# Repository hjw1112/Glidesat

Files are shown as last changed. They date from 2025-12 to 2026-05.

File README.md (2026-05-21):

# Glidesat
Custom devboard with additional components for ESA cansat competition. 

This PCB is for ESA cansat competition and I made it because I thought premade devboards like rp pico is too big and limiting for my team's goal. So I made this devboard to save as much space as possible and to connect to CM4 module for image processing. 

It is most complex PCB project so it was quite difficult to work on it, but with some help from background knowledge from previous projects, i think it went smoothly :)

Here are screenshots of PCB Design

## PCB Design
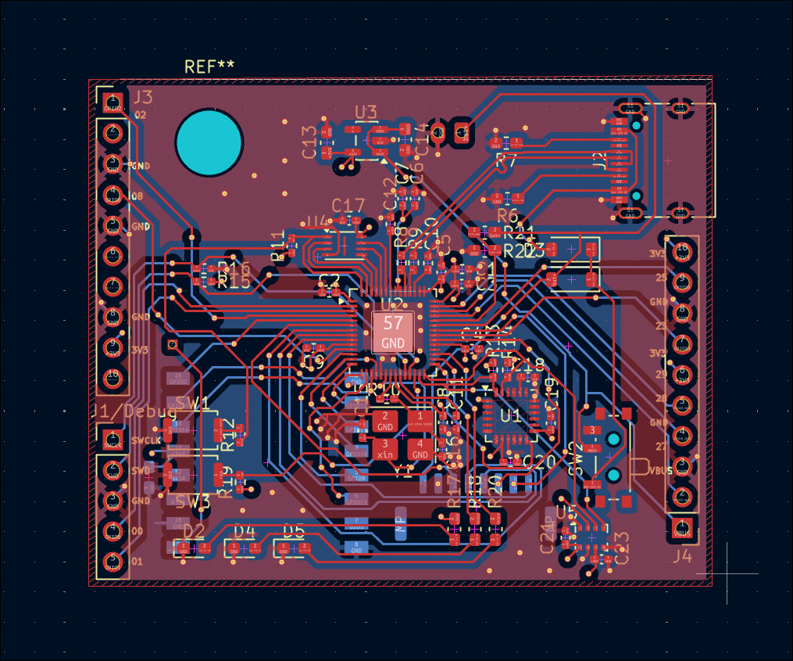
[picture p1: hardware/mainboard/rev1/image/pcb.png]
PCB


## Schematic
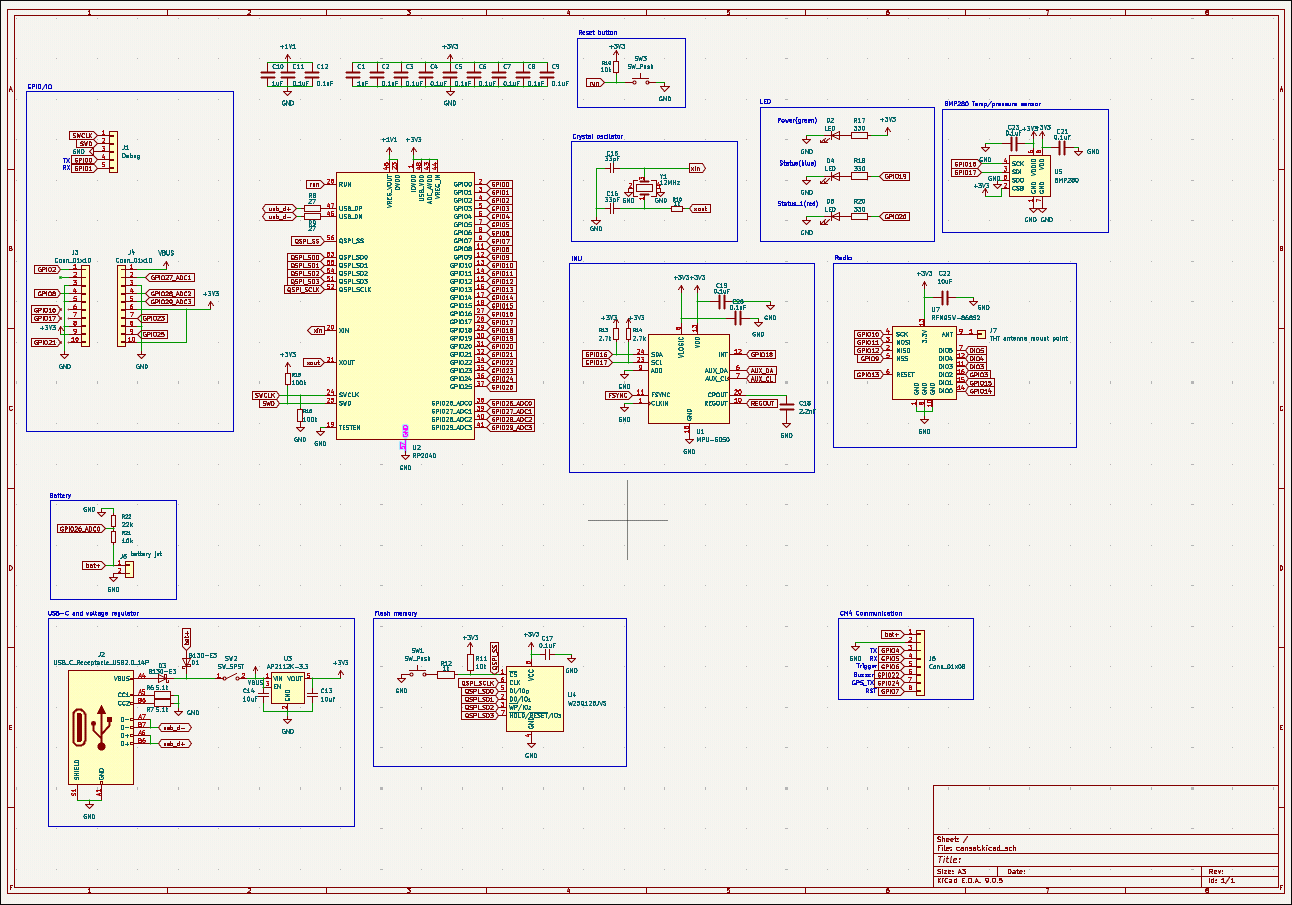
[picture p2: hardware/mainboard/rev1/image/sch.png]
Schematic


## 3D View
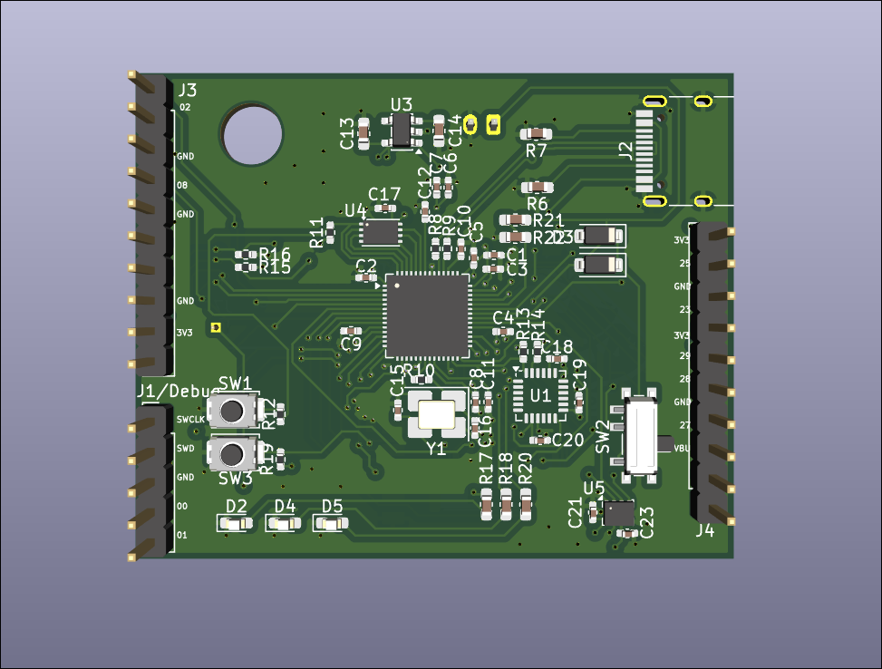
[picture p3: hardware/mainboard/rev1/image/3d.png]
3D View


## Soldered PCB

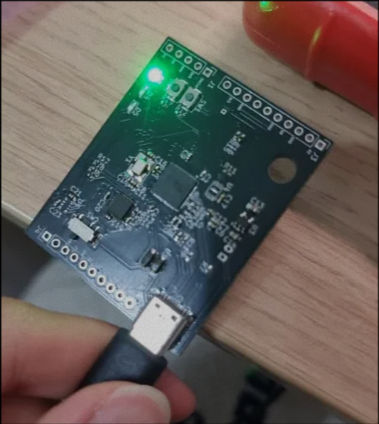
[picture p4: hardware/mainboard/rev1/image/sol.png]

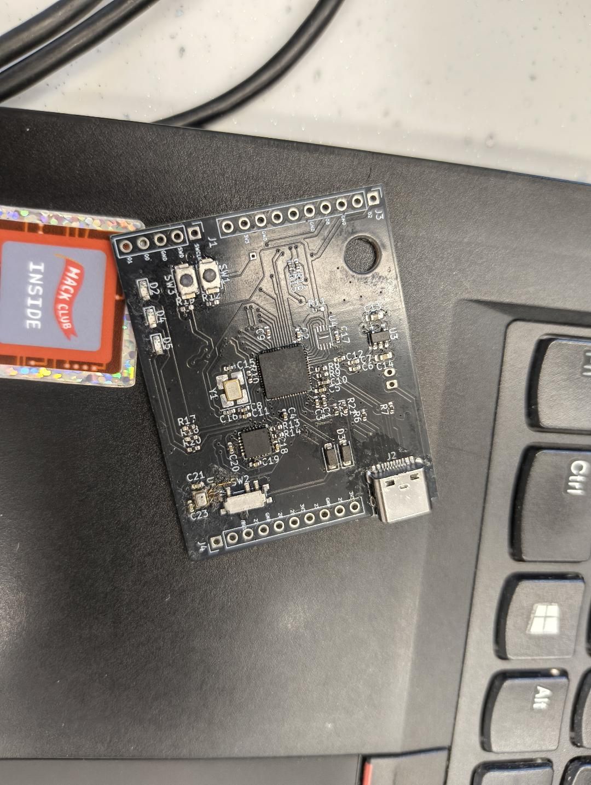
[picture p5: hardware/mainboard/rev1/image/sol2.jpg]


---

## BOM

| Component | Quantity |  Price | Net price | Source | | |
|:---|---:|:---|:---|:---|:---|:---|
| Capacitor 1uF | 100 |  0.0015 |  0.15 | https://www.lcsc.com/product-detail/C14445.html | | |
| Capacitor 0.1uF | 100 |  0.0011 |  0.11 | https://www.lcsc.com/product-detail/C1525.html | | |
| Capacitor 10uF | 50 |  0.0051 |  0.26 | https://www.lcsc.com/product-detail/C19702.html | | |
| Capacitor 33pF | 100 |  0.0030 |  0.30 | https://www.lcsc.com/product-detail/C70465.html | | |
| Capacitor 2.2nF | 100 |  0.0033 |  0.33 | https://www.lcsc.com/product-detail/C84703.html | | |
| B130-E3 | 10 |  0.0435 |  0.44 | https://www.lcsc.com/product-detail/C129191.html | | |
| LED(RED) | 100 |  0.0048 |  0.48 | https://www.lcsc.com/product-detail/C19171390.html | | |
| LED(GREEN) | 100 |  0.0047 |  0.47 | https://www.lcsc.com/product-detail/C19273151.html | | |
| LED(BLUE) | 100 |  0.0036 |  0.36 | https://www.lcsc.com/product-detail/C19171394.html | | |
| USB_C_Receptacle_USB2.0_14P | 5 |  0.1533 |  0.77 | https://www.lcsc.com/product-detail/C165948.html | | |
| Header pins | 10 |  0.0150 |  0.15 | https://www.lcsc.com/product-detail/C42431810.html | | |
| BM08B-GHS-TBT(LF)(SN) | 5 |  0.3074 |  1.54 | https://www.lcsc.com/product-detail/C133062.html | | |
| Resistor 5.1k 0603 | 100 |  0.0008 |  0.08 | https://www.lcsc.com/product-detail/C2907044.html | | |
| Resistor 27k 0402 | 100 |  0.0006 |  0.06 | https://www.lcsc.com/product-detail/C138017.html | | |
| Resistor 1k 0402 | 100 |  0.0006 |  0.06 | https://www.lcsc.com/product-detail/C106235.html | | |
| Resistor 10k 0402 | 100 |  0.0006 |  0.06 | https://www.lcsc.com/product-detail/C60490.html | | |
| Resistor 2.7k 0402 | 100 |  0.0007 |  0.07 | https://www.lcsc.com/product-detail/C138017.html | | |
| Resistor 100k 0402 | 100 |  0.0006 |  0.06 | https://www.lcsc.com/product-detail/C60491.html | | |
| Resistor 330 0603 | 100 |  0.0010 |  0.10 | https://www.lcsc.com/product-detail/C23138.html | | |
| Resistor 220 0603 | 100 |  0.0010 |  0.10 | https://www.lcsc.com/product-detail/C22962.html | | |
| Resistor 10k 0603 | 100 |  0.0010 |  0.10 | https://www.lcsc.com/product-detail/C98220.html | | |
| Resistor 22k 0603 | 100 |  0.0011 |  0.11 | https://www.lcsc.com/product-detail/C114065.html | | |
| SW_Push(XUNPU TS-1088-AR02016) | 10 |  0.0369 |  0.37 | https://www.lcsc.com/product-detail/C720477.html | | |
| SW_SPST(C&K PCM12SMTR) | 3 |  1.0445 |  3.13 | https://www.lcsc.com/product-detail/C221841.html | | |
| MPU-6050 | 3 |  5.9586 |  17.88 | https://www.lcsc.com/product-detail/C24112.html | | |
| RP2040 | 3 |  0.8250 |  2.48 | https://www.lcsc.com/product-detail/C2040.html | | |
| AP2112K-3.3 | 5 |  0.0803 |  0.40 | https://www.lcsc.com/product-detail/C23380830.html | | |
| W25Q128JVSIQ | 3 |  1.4281 |  4.28 | https://www.lcsc.com/product-detail/C97521.html | | |
| BMP280 | 2 |  5.2477 |  10.50 | https://www.lcsc.com/product-detail/C83291.html | | |
| RFM95W-868S2 | 1 |  9.5500 |  9.55 | https://www.tme.eu/sk/en/details/rfm95cw-868s2/rf-modules/hope-microelectronics/?brutto=1 | | |
| X322512MSB4SI | 10 |  0.0592 |  0.59 | https://www.lcsc.com/product-detail/C9002.html | | |
| | | | | | | |
| Shipping LCSC | | |  8.49 | | | |
| Discount | | |  6.00 | | Component total |  64.47 |
| Shipping from time.eu | | |  6.64 | | | |
| | | | | | | |
| PCB | | |  9.70 | JLCPCB | | |
| Shipping(GSDL) | | |  7.18 | | | |
| Tax | | |  2.58 | | PCB Total |  19.46 |
| | | | | | | |
| | | | | | | |
| TOTAL | | |  83.93EUR (about $98.82) | | | |

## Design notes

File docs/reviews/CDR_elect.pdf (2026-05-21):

## 7 Electronic Design

### 7.1 General Design

In the Preliminary Design Review (PDR), we used a 4-board system with Linux and GPS modules separated. However, we concluded that interference between RF modules is lower than interference with the Linux board. We managed to integrate the GPS module onto the mainboard. The number of boards remains the same, but the GPS module is now on the mainboard.

1. Mainboard – System control, sensor reading, radio communication, logic
2. Motor Control Board – Actuator control
3. Camera Board – High-resolution image capture
4. Linux Module – Commercial Linux module

This architecture separates the control system (mainboard), high-speed camera/Linux operation, and high-voltage motor control. This reduces electrical interference between sub-systems and improves communication reliability.

### 7.1.1 Design Evolution and Component Selection

At the start of the project, multiple MCUs were evaluated: Atmel ATmega series (Arduino equivalent), STM32, ESP32, and RP2040.

- Atmel chips were rejected due to insufficient processing power and memory to handle multiple peripherals reliably.
- STM32 and ESP32 were considered but were more power-hungry, more complex, and exceeded the performance needs of Glidesat.
- RP2040 was selected due to its dual-core processing, multiple communication interfaces, low power consumption, and strong community support. Despite QFN package soldering difficulties, the performance-to-power ratio justified its selection.

### 7.1.2 Board Design

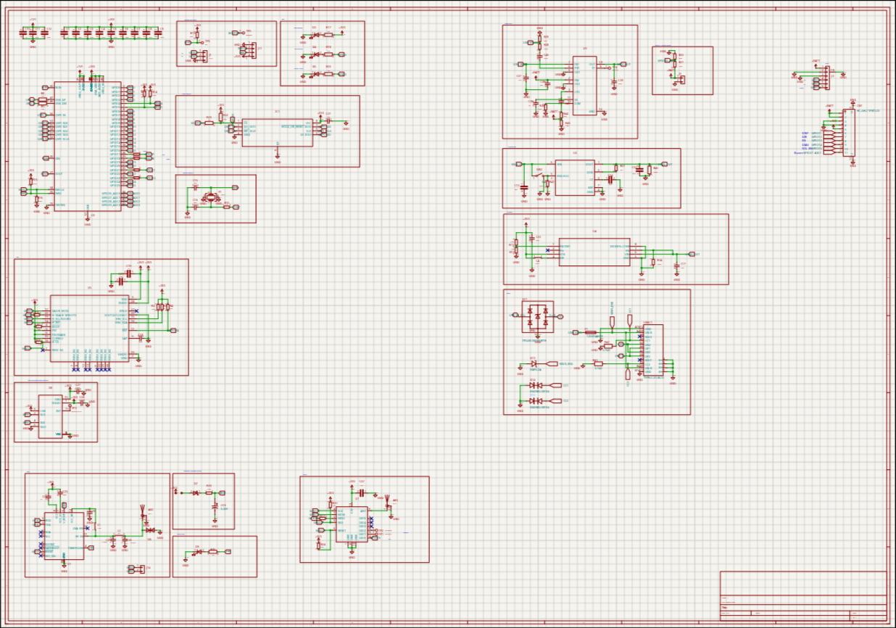
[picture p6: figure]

Figure 8: Schematic Design

The mainboard is a 4-layer PCB. Core processing is handled by the RP2040 SoC. Complementary components:

- Flash memory – W25Q128JVS
- Crystal oscillator – X322512MSB4SI

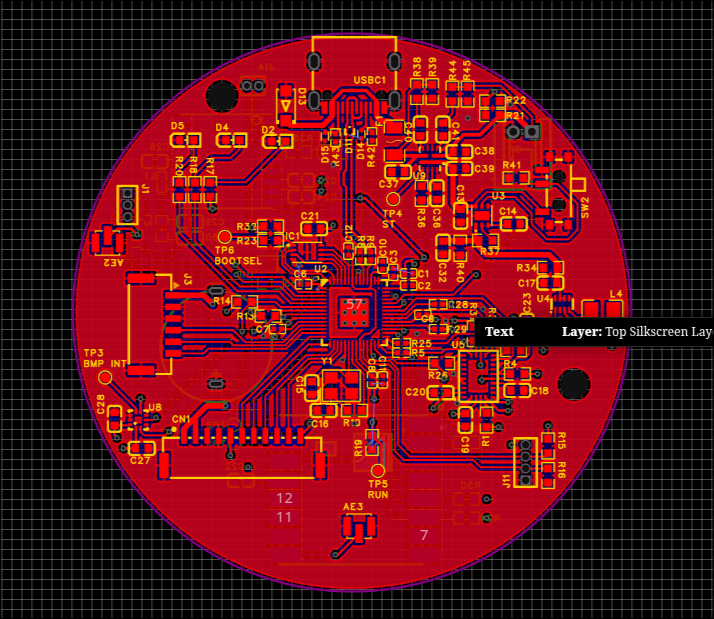
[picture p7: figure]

Figure 9: PCB Design

- Voltage regulator – AP2112K-3.3
- Power MUX – TPS2121RUXR
- Load switch – TPS22810DRVR
- Power MUX allows USB-C powering for flashing/testing.
- Load switch protects against high current draw which could damage a simple switch.
Sensor | Unit
Barometric Pressure Temperature IMU (Initial Measurement Unit) Battery Voltage Monitor | BMP388 BMP388 BNO085 GPIO ADC

Sensors are placed away from heat-generating components, with ventilation openings near them, to minimize thermal distortion.
IMU Selection: MPU-6050 was replaced with BNO085 to obtain 9-DOF measurements (magnetometer included) to prevent yaw drift. BNO085 offers internal sensor fusion, higher sampling rate, reduced MCU load, and additional data (gravity vector, linear acceleration) useful for landing detection and stable glider steering. ICM-20948 and others were considered but lacked magnetometers or required external fusion.
Barometric Sensor Selection: BMP388 was chosen for its precision (important for altitude monitoring without a camera), low pressure noise (useful during oscillating descent), high sampling rate ( 200 Hz), temperature compensation, compact size, dynamic pressure range (500 m– 9000 m), and low power consumption.

### 7.1.3 Radio Communications

RFM95W-868S2 LoRa transceiver is used via SPI to transmit telemetry to the ground station, including altitude, temperature, GPS coordinates, system status, and image capture status.

### 7.1.4 GPS

MAX-M10S-00B was selected for its multi-constellation support (higher accuracy), lower power consumption (20 mA vs 45 mA for older M10M), better sensitivity, and faster fix time.

### 7.1.5 Camera/Linux Board

For imaging, the Luckfox Pico Mini and MIS5001 5MP Wide-Angle Camera Module were chosen.

- Raspberry Pi Compute Module 4 was replaced due to size and weight.
- Camera resolution was reduced to 5 MP due to the Pico Mini’s 2-lane MIPI CSI limitation.
- High-resolution capture could not be done directly via RP2040 due to limited RAM, insufficient SPI bandwidth, and lack of MIPI CSI support.
- The Linux board triggers the camera via UART communication with the mainboard.

### 7.1.6 Motor Control Board

- Drives paraglider motors, regulates power for actuators, and includes a buzzer for recovery system (higher voltage requirement).
- Separation from mainboard prevents high-current electrical noise from affecting sensors or LoRa modules.
- Micro metal gear motor with encoder controlled via DRV8833 motor driver.

### 7.2 Power Supply

### 7.2.1 Power Source

Glidesat is powered by a rechargeable LiPo battery. Two options were considered: single-cell (3.7 V nominal) and dual-cell (7.4 V nominal).

- Dual-cell reduces current for the same power, improving wiring efficiency and allowing efficient buck conversion.
- Design considerations for dual-cell include charging circuit complexity and over-voltage protection.
- A dual-cell 2700–3000 mAh battery was selected to cover a 4-hour mission with safety margin ( 20 Wh total energy requirement).

### 7.2.2 Power Regulation

- Most electronics operate at 3.3 V (RP2040 and sensors) using a high-efficiency buck converter.
- Battery voltage monitored via mainboard ADC.
- Distribution via JST GH connectors to prevent disconnection.
- 3.3 V for mainboard components, raw 7.4 V to motor and Linux boards; 5 V regulated onboard for camera and motors.

### 7.3 Communication System

Glidesat communicates with the ground station via RFM95W-868S2 LoRa transceiver. The system supports bi-directional communication for telemetry and command reception.
Data transmitted from ;’[]:
- Altitude
- Temperature
- GPS coordinates
- Battery voltage

- System status
- Camera status

Data received by Glidesat:

- Motor direction
- Motor speed
- Recovery system activation

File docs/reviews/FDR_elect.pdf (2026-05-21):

## 7 Electronic Construction

### 7.1 System Overview

The electronic system of Glidesat consists of three custom-designed printed circuit boards (PCBs): a mainboard, a motor control board, and a Linux board. Off-the-shelf solutions were evaluated but rejected because their physical dimensions were not suitable for the 66 mm diameter CanSat form factor and they provided no isolation between high-current actuator paths and sensitive sensor/communication circuitry. Splitting the electronics across three boards allowed the us to fit all required functionality within the diameter limit while achieving electrical isolation between subsystems.3

### 7.1.1 Architecture

- Mainboard – flight computer, sensor, LoRa telemetry, GPS, data logging, power distribution.
- Motor control board – parafoil actuator drive, burn wire mechanism, buzzer recovery system.
- Linux board – Linux SBC, high-resolution imaging, onboard image storage.

This separation isolates the high-voltage, high-noise actuator paths on the motor board from the sensitive GPS, IMU, and LoRa circuitry on the mainboard. Each board operates on its own regulated power rail, providing independent fault domains.

### 7.1.2 Block Diagram

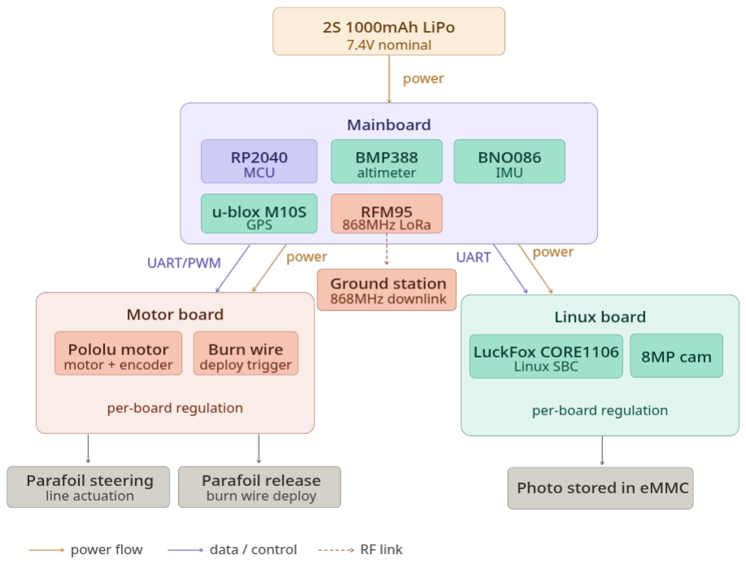
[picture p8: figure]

Figure 16: Block Diagram

### 7.2 PCB Design

### 7.2.1 Board Specifications

All boards are circular with a diameter of 60 mm and use M2.5 mounting holes positioned 15 mm from the centre of the board. The mainboard and Linux board use a four-layer stackup with the following layer assignment:

- L1 – signal

- L2 – ground plane
- L3 – power (with a dedicated region for raw battery voltage on the mainboard to improve current handling)
- L4 – signal

The motor board uses a two-layer stackup sufficient for its lower component density.

### 7.2.2 PCB Images

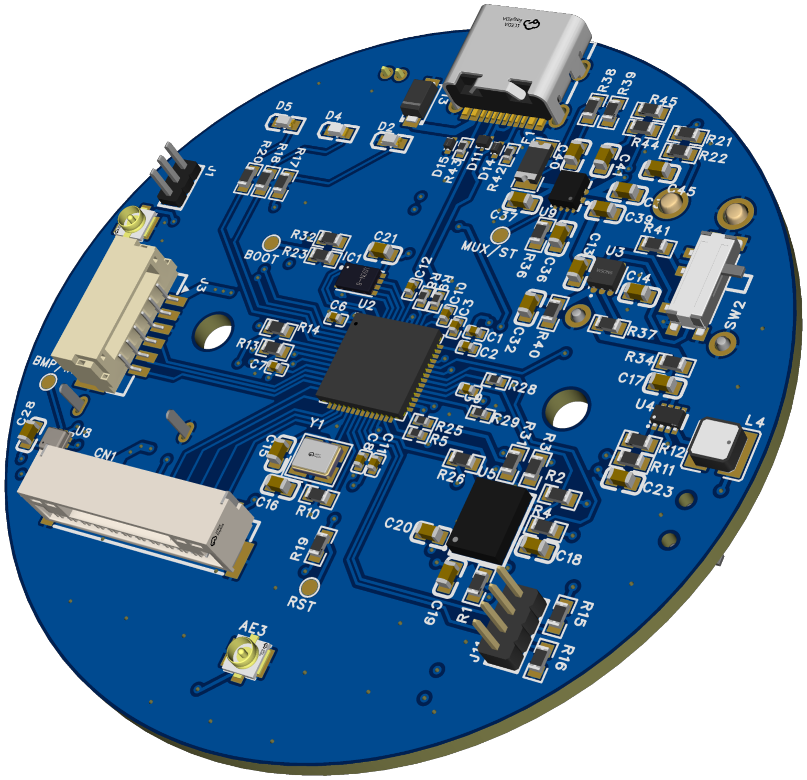
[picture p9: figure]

Figure 17: Mainboard

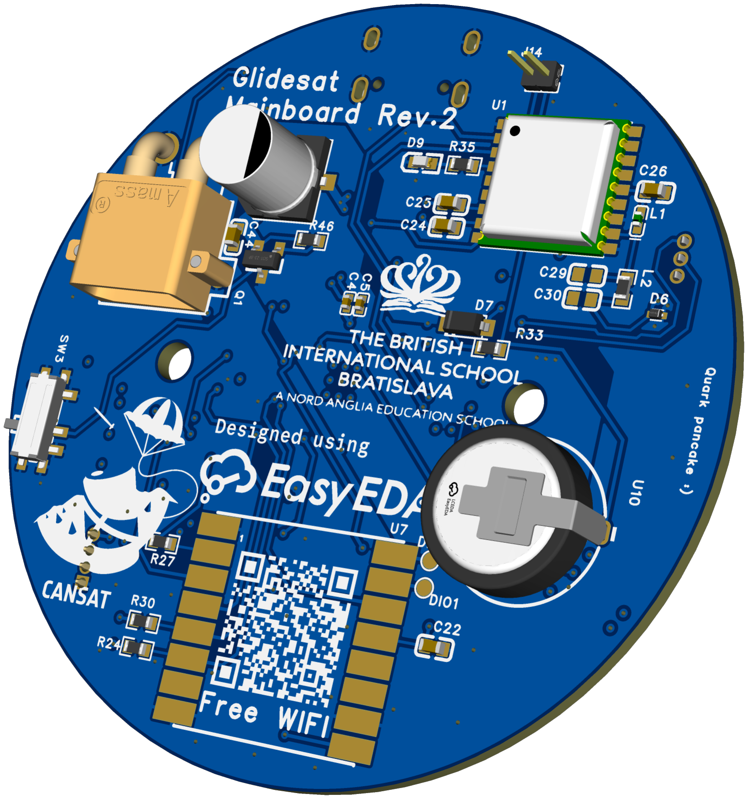
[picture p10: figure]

Figure 18: Mainboard(bottom)

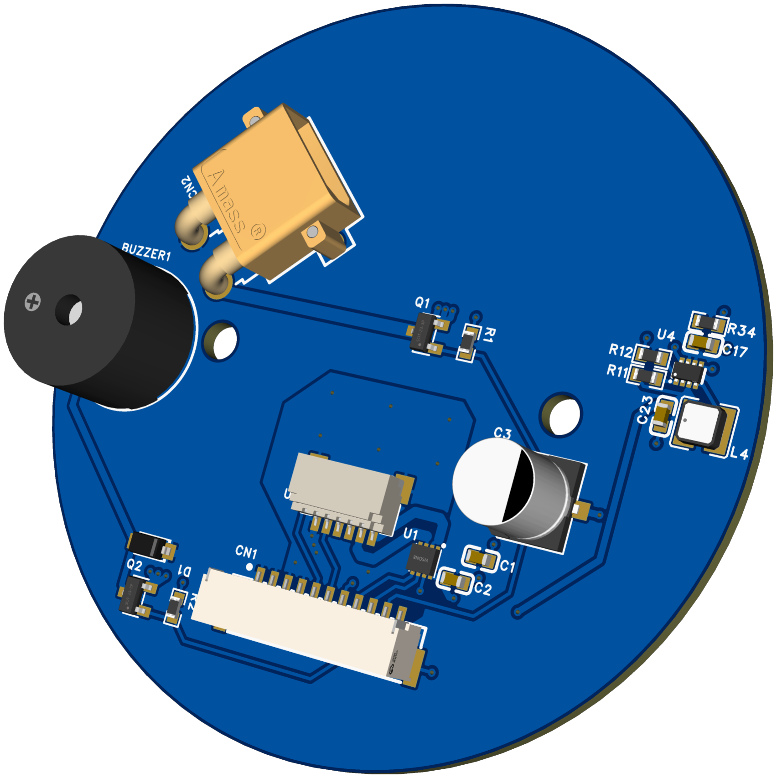
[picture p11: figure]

Figure 19: Motor Board

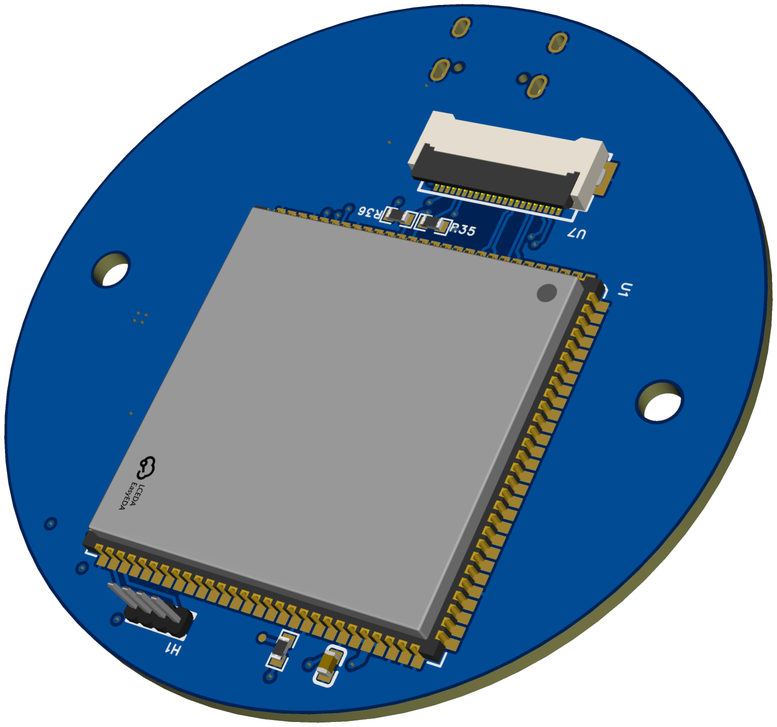
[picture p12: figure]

Figure 20: Linux Board

### 7.2.3 Board-to-Board Connections

JST-GH 1.25 mm pitch connectors were selected for all inter-board signal connections. The positive locking mechanism prevents disconnection under vibration during rocket ascent and mechanical shock on landing – a failure mode that unlatched connectors such as JST-PH or Dupont headers are susceptible to. All cables include strain relief at both ends.

### 7.3 Subsystem Descriptions

### 7.3.1 Flight Computer – RP2040

The RP2040 dual-core Cortex-M0+ SoC act as the flight computer.
Peripheral connections: SPI for RFM95W LoRa module and W25Q16JV flash memory; I2C for BMP388 and BNO086; UART for u-blox MAX-M10S and LuckFox Core1106; PWM for DRV8838 motor driver; GPIO ADC for battery voltage monitoring. A 12 MHz crystal oscillator provides the system clock reference.

### 7.3.2 Sensor Subsystem

Table 6: Sensor subsystem summary

Component | Function | Interface | Key Spec
BMP388 | Barometer, temperature | SPI/I2C | ±0.5 m altitude resolution
BNO086 | 9-DOF IMU | I2C | On-chip sensor fusion, quaternion output
u-blox M10S | GPS / GNSS | UART | Concurrent GNSS, 9 mA typical
IMX415 | Camera sensor | MIPI CSI | 8 MP, via LuckFox Core1106

BMP388 The BMP388 provides barometric altitude and temperature measurements. Its altitude resolution of ±0.5 m and low noise floor are important for monitoring the gliding descent without camera assistance. The higher sampling rate of up to 200 Hz and improved temperature compensation over its alternatives make it well suited to the Glidesat body that oscillates during descent.

BNO086 A 9-DOF IMU with on-chip sensor fusion was required because a 6-DOF IMU without a magnetometer causes yaw drift, which leads to mis-steering of the parafoil. The BNO086 outputs calibrated data directly, removing the need for an external fusion algorithm, reducing MCU load, and removing the risk of incorrect manual calibration.

u-blox MAX-M10S The MAX-M10S supports concurrent reception of GPS, GLONASS, Galileo, and BeiDou signals, improving position accuracy and fix reliability. At approximately 9 mA typical current consumption it draws significantly less power than the Neo-6M module used in earlier revisions. A 0.33 F supercapacitor on the mainboard maintains the module’s hot-start data and real-time clock during brief power interruptions, reducing position reacquisition time from approximately 30 s (cold start) to approximately 1 s (hot start).

### 7.3.3 Communication Subsystem

The RFM95W-868S2 LoRa transceiver operates at 868 MHz, which is within the licence-free ISM band across the European Union. The module is connected via SPI and implements a bi-directional link:

- Downlink (CanSat → ground station): altitude, temperature, GPS coordinates, battery voltage, system status, camera capture status.
- Uplink (ground station → CanSat): motor direction, motor speed, recovery system activation.

All telemetry is simultaneously logged to the W25Q16JV 16 Mbit flash memory, providing a complete flight data record independent of the radio link.
Antenna note: During PCB layout review it was identified that impedance matching for the RFM95W antenna trace was not implemented and the copper ground plane was not cleared under the antenna connector. This is expected to introduce approximately 1–3 dB of additional insertion loss due to signal reflection. The ground station uses a 13 dBi Yagi antenna, which provides sufficient gain margin to compensate for this loss. The link was confirmed operational during range testing. Also, a empty pi network with 0Ω resistor was implemented for post-impedance matching. So we can tune the impedance if we need extra range.

### 7.3.4 Actuation Subsystem

The motor board drives a Pololu 100:1 micro metal gearmotor with encoder using a DRV8838 single H-bridge motor driver. The 100:1 gear ratio was selected to provide sufficient torque to pull parafoil control lines under canopy load at operational descent speeds. The encoder provides closed-loop position feedback to the RP2040 control loop. The DRV8838 supports up to 1.8 A peak current, which is sufficient for the selected motor, and its WSON-8 2×2 mm package contributes to the compact board layout.
The burn wire deployment mechanism is triggered by a pair of AO3400A N-channel MOSFETs driven directly from RP2040 GPIO. The MOSFET pair allows reliable high-current switching at logiclevel gate voltage without the bulk and mechanical wear of a relay. Deployment confirmation is provided by monitoring current draw or encoder movement after trigger.
A buzzer is included on the motor board for post-landing recovery assistance. It is placed on the motor board because the higher supply voltage already present on that board is required for audible output level.

### 7.3.5 Imaging Subsystem

The LuckFox Core1106 runs a Linux operating system and interfaces with the IMX415 8 MP camera sensor via a two-lane MIPI CSI connection. Images are stored to the onboard eMMC. The LuckFox receives image capture commands from the RP2040 over UART and responds with capture status. Because Linux boot time is approximately 20–40 s, the Linux board is powered on and verified before launch to avoid mid-flight boot delay.

### 7.3.6 Power Subsystem

The system is powered by a 2S 1000 mAh LiPo battery with a nominal voltage of 7.4 V. A TPS2121 power multiplexer on the mainboard allows automatic switchover between battery and USB-C supply, enabling firmware development and sensor testing without connecting the flight battery.
Each board has a dedicated TPS629206 synchronous buck regulator providing the following voltage rails:
- Mainboard: 3.3 V for RP2040, sensors, and LoRa module.
- Motor board: 7.4 V raw battery voltage for motor and burn wire; 3.3 V regulated for logic.
- Linux board: 5 V for LuckFox Core1106.

Per-board regulation ensures that motor switching noise and current spikes on the motor board cannot affect the sensitive GPS, IMU, and LoRa rails on the mainboard. Battery voltage is monitored continuously by the RP2040 ADC using voltage divider. The XT30 battery connector is rated for 30 A continuous, providing a large margin over the 1.3 A peak system current draw.

### 7.3.7 Protective and Reliability Features

Several protective measures were implemented to improve robustness under the mechanical and electrical stresses of the mission environment.

Table 7: Protective and reliability features

Feature | Component | Protection provided
Overcurrent fuse | 1206T4A63V | Trips at 4 A on main power input; protects against
wiring faults and short circuits.
ESD protection | USBLC6-2SC6 | TVS
diode

Clamps electrostatic discharge on USB lines during ground handling and programming.

GPS backup power | 0.33 F supercapacitor | Maintains MAX-M10S hot-start data and RTC
during brief power interruptions; reduces reacquisition time from ∼30 s to ∼1 s.
Locking connectors | JST-GH 1.25 mm | Positive locking prevents vibration-induced dis-
connection during ascent and landing impact.

Battery connector
margin
XT30 | 30 A rating versus 1.3 A actual peak; eliminates
contact resistance and heating concern.

Per-board power isolation

TPS629206 per board Motor switching noise and fault conditions are contained to the motor board and cannot affect sensor or comms rails.

Decoupling capacitors

100 nF / 1 µF per IC Bulk and bypass capacitors on every IC supply pin suppress transient voltage spikes.

### 7.4 Component Selection

### 7.4.1 Selection Criteria and Weighting

All key component selections were evaluated against seven criteria using a weighted scoring matrix. The criteria and their assigned weights are listed in Table 8.

Table 8: Selection criteria and weights

Criterion | Weight | Rationale
Reliability | 3 | Flight-critical; no recovery if electronics fail mid-descent.
Performance | 3 | Directly affects mission success (navigation accuracy, link range).
Power consumption | 2 | Limited battery capacity; sleep modes required for 4 h operation.
Size | 2 | 60 mm board diameter constraint.
Ease of integration | 2 | Limited development time.
Cost | 1 | Secondary to reliability for this application.
Availability | 1 | All parts can be sourced from various sellers.

Scores from 1 to 5 were assigned for each criterion and each option. The weighted total is the sum of score × weight across all criteria. The chosen part corresponds to the highest weighted total in

every case.

### 7.4.2 Shortened Decision Table

Table 9: Electronics component selection — Mainboard

Component | Chosen part | Alternative(s) | Reasoning
MCU | RP2040 | STM32, ATmega | Dual Cortex-M0+ cores, large community, cheap, PIO for
custom peripherals
GPS | u-blox | MAX-
M10S

Neo-M8N, BN-880 Low power (9 mA), compact package, concurrent GNSS, proven reliability
IMU | BNO086 | BNO085, MPU-6050,
ICM-42688

On-chip sensor fusion (no extra MCU load), low idle power, interactive calibration
Barometer | BMP388 | MS5611, BMP280 | ±0.5 m resolution, lower noise floor, low power
LoRa | RFM95W-868S2 | SX1276, NRF24L01 | 868 MHz legal in EU, long range, module reduces RF lay-
out complexity
Flash | W25Q16JV | — | 16 Mbit external flash for telemetry and code; RP2040
lacks internal flash
Power MUX | TPS2121 | Diode, manual switch Automatic mux between battery and USB; allows devel-
opment without battery
Supercap | 0.33 F | — | Enables M10S hot start, reducing position acquisition
time
Load switch | TPS22810 | MOSFET, | bulky
switch

Limits excessive current; allows smaller switch with low current rating

Table 10: Electronics component selection — Motor Board, Linux Board, and General

Component | Chosen part | Alternative(s) | Reasoning

Motor Board

Motor driver | DRV8838 | L298N, TB6612 | Single H-bridge in WSON-8 package; 1.8 A peak,
sufficient for our motor
N-MOSFET | AO3400A ×2 | Relay, BJT | Reliable high-current switching for buzzer and burn
wire

Linux Board

Linux SBC | Luckfox Core 1106 | RPI | Zero | 2W,
ESP32-S3

Built-in MIPI CSI for camera; smaller and lower power than Pi Zero

General

ESD protection | USBLC6-2SC6 TVS Diode
— | Prevents electrostatic discharge damage during
handling
Buck regulator | TPS629206 | LM1117, AMS1117 | Higher efficiency than linear regulators
B2B connector | JST-GH | JST-PH, SH, etc. | Locking mechanism, reliability
Battery conn. | XT30 | JST, screw terminal | Rated for 30 A, massive safety margin, reliable

### 7.5 Power Budget

### 7.5.1 Current Consumption

Table 11 lists the estimated current draw for each component in active and sleep states. All values are datasheet typical figures unless noted as measured.

Table 11: Current consumption per component

Board | Component | Active (mA) | Sleep (mA)
5*Mainboard – 3.3 V | RP2040 | 25 | 2
| BMP388 | 3 | 0.1
| BNO086 | 6 | 1
| u-blox M10S | 25 | 15
| RFM95W | 30 | 0.2
2*Motor board – 7.4 V | DC motor | 150 | 5
| Burn wire | 0 | 0
2*Linux board – 5 V | LuckFox Core1106 | 400 | 10
| Camera (IMX415) | 50 | 0
Regulators (all boards) | 3× TPS629206 | 30 | 30
Total | | 719 | 63

### 7.5.2 Mission Profile Calculation

The mission is modelled as 30 min active followed by 3 h 30 min in sleep state. The active duration is a conservative worst-case estimate; typical active time is expected to be shorter.

Qactive = 0.5 h × 719 mA = 359.5 mAh Qsleep = 3.5 h × 63 mA = 220.5 mAh Qtotal = 359.5 + 220.5 = 580 mAh

Assuming a depth of discharge of 70 % to preserve battery longevity:

Qusable = 1000 mAh × 0.70 = 700 mAh

Qmargin = 700 − 580 = 120 mAh (17 %)

The 120 mAh safety margin is considered sufficient for the 4 h mission requirement.

### 7.5.3 Battery Selection

The Spektrum Smart G2 2S 1000 mAh 50C LiPo was selected. The reduction from the 2700 mAh specified at CDR was made possible by the sleep/active power analysis and change in cell number from 1 to 2, which showed that the LuckFox and motor consuming the majority of current are idle for most of the mission. The 50C discharge rating supports a peak current of 50 A, exceeding the 1.3 A actual peak draw (1.3C). The physical dimensions of the pack are compatible with the CanSat body.

### 7.6 Design Evolution and Revision History

### 7.6.1 Changes from PDR and CDR

Table 12 summarises all significant design changes made since the PDR and CDR submissions.

Table 12: Design evolution summary

Item | PDR/CDR | FDR | Reason
GPS loca- tion | Separate board | Mainboard | Mainboard placement keeps Linux board at bot- tom; GPS antenna faces top. LoRa/GPS interfer- ence negligible at achievable separation.
Camera SBC | RPi CM4 → LuckFox Pico Mini | LuckFox Core1106 | CM4 too large/heavy; Pico Mini lacked comput- ing power; Core1106 adds eMMC and robust form factor.
Camera sensor | Arducam 477P → MIS5001 5 MP
IMX415 8 MP | Higher resolution improves landing zone documen-
| | | tation.
IMU | MPU-6050 (6-DOF) | BNO086 | (9-
| | DOF) | Magnetometer prevents yaw drift; on-chip fusion reduces MCU load.
Barometer | BMP280 | BMP388 | ±0.5 m vs ±1 m resolution; lower noise; higher sample rate.
GPS mod- ule | Neo-6M | u-blox | MAX-
| | M10S | Concurrent GNSS; 9 mA vs 45 mA; faster fix time.

Motor
driver
DRV8833 | DRV8838 | Single H-bridge sufficient; smaller WSON-8 pack- age.
Battery | 1S 2700 mAh (CDR) | 2S 1000 mAh | Sleep/active analysis confirms sufficiency with 120 mAh margin; significant weight saving.
Board count | 4 boards (separate GPS) | 3 custom + 1 commercial | GPS integrated onto mainboard; camera module is commercial.

### 7.6.2 Revision 1 – Objectives and Findings

The objectives of Revision 1 were to validate the fundamental PCB design: RP2040 bring-up in multisensor configuration, SPI / I2C / UART interface verification, power regulation testing, and LoRa radio operation.

### 7.6.3 Revision 2 – Improvements

Revision 2 implements all lessons from Rev1 testing and upgrades all sensor components to their final flight versions.

Table 13: Test summary

Test | What was verified | Revision | Status
RP2040 bring-up | MCU boot, peripheral init | Rev1 | Pass
Sensor communication | I2C/SPI responses | Rev1 | Pass
LoRa link | Range, RSSI, packet loss | Rev1 | Pass
GPS fix | Fix time, accuracy | Rev2 | Pass
Motor + encoder | Closed-loop operation | Rev2 | Pass
Burn wire trigger | Fire time, current | Rev2 | Pass
Power measurement | Current draw vs estimate | Rev2 | Pass
Full system integration | 3-board combined test | Rev2 | Pass

### 7.7 Testing and Validation

### 7.7.1 Test Summary

### 7.8 Risk Assessment

### 7.8.1 Risk Table

Table 14: Electronics risk assessment

Risk | Likelihood Impact Mitigation

Motor board noise affecting sensors

Medium | High | Per-board power regulation and ground plane iso-
| lation.

Burn wire fails to trigger

Low | High | Bench-tested before flight; firmware watchdog
triggers backup after timeout if descent rate does
| not decrease.

LoRa link lost during
descent
Low | High | 868 MHz chosen for range; all telemetry logged to
onboard flash memory independently of radio link.
LuckFox fails to boot | Low | Medium All flight-critical functions reside on RP2040;
LuckFox failure does not abort the mission.

Battery undervoltage
during peak draw
Low | High | Decoupling capacitors on each board; motor stall
protection in firmware; 120 mAh safety margin.

Connector disconnection on landing

Low | High | JST-GH locking connectors; XT30 battery con-
nector; strain relief on all inter-board cables.

ESD damage during
handling

Medium Medium USBLC6-2SC6 TVS diode on USB lines; ESD handling procedures during integration.

Antenna impedance
mismatch
High | Low | Ground plane not cleared under antenna connec-
tor; estimated 1–3 dB loss compensated by 13 dBi Yagi at ground station; confirmed operational in
| range test.

### 7.8.2 Residual Risks

The antenna impedance mismatch remains unresolved in Revision 2. This is considered acceptable based on the range test results demonstrating reliable link operation, and the availability of a high-gain ground station antenna. Should field testing reveal insufficient range, the issue will be corrected with empty pi network.

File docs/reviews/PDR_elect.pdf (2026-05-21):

## 7 Electronic Design

### 7.1 General Design

The electronic system of Glidesat is divided into 4 boards. 1 mainboard and 4 sub-boards.

1. Mainboard - system control, sensor reading, radio communication, logics
2. Motor Control Board - actuator control
3. Camera Board – high resolution image taking and onboard data storage
4. GPS Module – commercial GPS module

This architecture allows us to separate the control system (mainboard), high speed camera operation, high voltage motor control, and high precision GPS. This separation reduces electrical interference between sub-systems and improves communication reliability. Communication between systems will use following standard interfaces: UART, I2C, SPI, PWM/GPIO.

### 7.1.1 Design Evolution and Component selections

In the beginning of the project, few MCUs were evaluated. Including the Atmel ATmega series (Arduino equivalent), STM32, ESP32, and RP2040. Atmel chips were rejected since they could not carry out multiple peripherals at the same time reliably, due to the lack of sufficient processing power and memory. STM32 and ESP32 chips were also considered but were found to consume more power, introduce unnecessary complexity, and exceed the performance requirements of our Glidesat application. The RP2040 SoC was selected as it offers dual-core processing power, multiple communication interfaces, low power consumption compared to higher end MCU such as STM32 or ESP32, and great community support and documentation. Although RP2040 is only available as QFN packages, which introduces soldering difficulties, the performance to power ratio advantages justifies the selection.

### 7.1.2 Board design

Complementary components: Flash memory – W25Q128JVS, Crystal oscillator - X322512MSB4SI, Voltage regulator – AP2112K-3.3

Sensor | Unit
Barometric pressure Temperature IMU (Initial Measurement Unit) Battery voltage monitor | BMP280 BMP280 MPU-6050 GPIO ADC

To minimise thermal distortion of environmental readings, sensors are placed in separate places with heat generating components, and ventilation opening will be placed near the sensors.
A LoRa transceiver is used for communication. It is connected via SPI and it is used to transmit telemetry data to the ground station. Including: Altitude, temperature, GPS coords, system status, image capture status. For GPS, the Neo-6M GPS module is used.
For camera module, we chose to integrate Raspberry Pi Compute Module 4(CM4) and Arducam 477P high-quality camera module for image capturing. In the beginning of the project, the camera system was planned to be controlled directly by RP2040 via SPI. However, this approach has been rejected since we needed a high resolution(10mp+) camera. The problem was limited RAM of RP2040 (and MCU in general), insufficient bandwidth of SPI for such high-resolution (No high res camera have SPI interface), and lack of native support of the MIPI CSI interface. To capture the high-resolution images, a Linux embedded computer was required. The Raspberry Pi Compute module 4 was therefore selected. The CM4 offers native MIPI CSI interface support, sufficient RAM, stable Linux camera drivers, and data storage via micro-SD card. CM4 will control the camera and trigger it by communicating with the mainboard via UART. There are two possible ways to operate CM4 are evaluated. The first option is operating continuously throughout the mission, and the second option

7

is turned on when needed using MOSFET. The first option can reduce power cycling and reliability but consume more power. However, the second option consumes less power, but it takes 20-40 seconds of time to boot the Linux system, and it is not highly reliable. Since reliability is a priority in this application, we decided to turn on the CM4 before launching and operate continuously throughout the flight.
The motor board will drive signals for paraglider motors, regulate power for actuators, and have a buzzer as part of the recovery system. The buzzer is added to the motor control board because it requires higher voltage which is already present in the board. Having a separated motor control board allows us to have high current paths separated from the mainboard and prevent electrical noises that might be present with high current paths from affecting sensors or LoRa modules, and it simplifies the PCB Design.

### 7.1.3 Prototype Mainboard Development (Mainboard Rev.1)

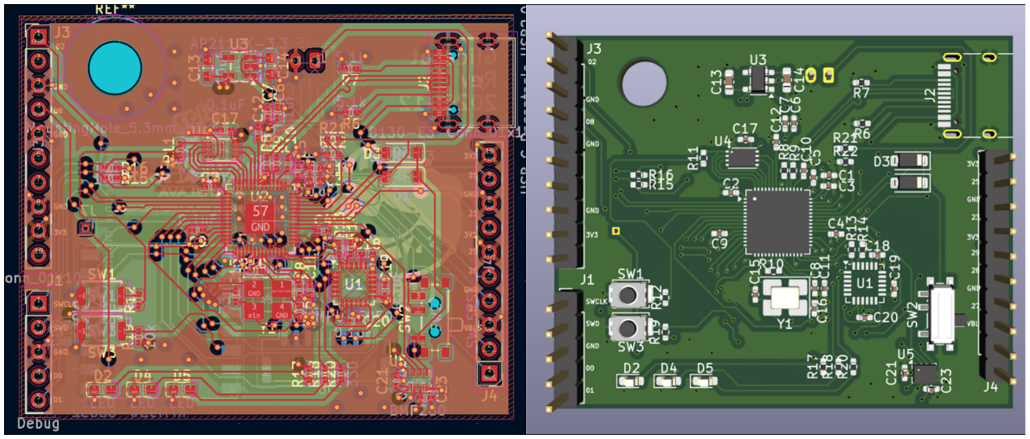
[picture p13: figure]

Figure 5: Prototype Mainboard

The first prototype of the mainboard was designed using Kicad, and we are currently waiting for the production.The objectives of Mainboard Rev.1 were to evaluate the general functionality of a designed PCB. Specifically, the RP2040 MCU in multi sensor configuration, verify SPI, I2C, and UART communication interfaces, test power regulation, test radio, etc. We spotted some flaws on PCB after submitting production via JLC PCB, but it should be okay since it is the first prototype.

### 7.1.4 Prototype Mainboard Development (Mainboard Rev.2)

After finishing Rev.1, we started to work on Rev.2 based on the mistakes we made in Rev.1. We planned pinout of the GPIO pins so we can keep pins organized and planned the board configuration. When we were working on Rev.1, we did not have clear board structure, so we only have a 01x08 JST connector in Rev.1
Also in Rev.1, we used MPU-6050 as our IMU. But after examining its capabilities, we found that it is not sufficient for controlling parafoil because it lacks a magnetometer which leads to the yaw drift. Thus, we will use 9-DOF IMU for Rev.2. Possibly MPU-9250 and ICM-20948.

### 7.2 Power Supply

The Glidesat is powered by a rechargeable lithium polymer battery system. Two options were evaluated. Single cell with nominal voltage 3.7V and double cell with 7.4V. Double cell systems offer higher voltage and reduced current for equal power consumption. However, it increases system complexity because of multiple voltage rails, has risk of overvoltage, more weight, and additional safety requirements for charging. Therefore, after evaluation, a single cell LiPo battery is chosen for Glidesat. Single cells are better since most electronics operate at 3.3V(RP2040, sensors, etc.), using a boost converter is simple and efficient, simplified charging, and reduced weight. Estimated power consumption: CM4 – 2W, Mainboard – 1W,Motor board and buzzer – 2W so total 5V . For mission of 1h 5W · 1h = 5Wh(safety margin of 2 − 5Wh)- therefore, a capacity between 2000mAh and 3000mAh battery is used. DC-DC boost converter generates higher voltage for CM4, actuators, and buzzer. A buck regulator generates 3.3V for RP2040. Battery voltage is monitored by the mainboard ADC.

8

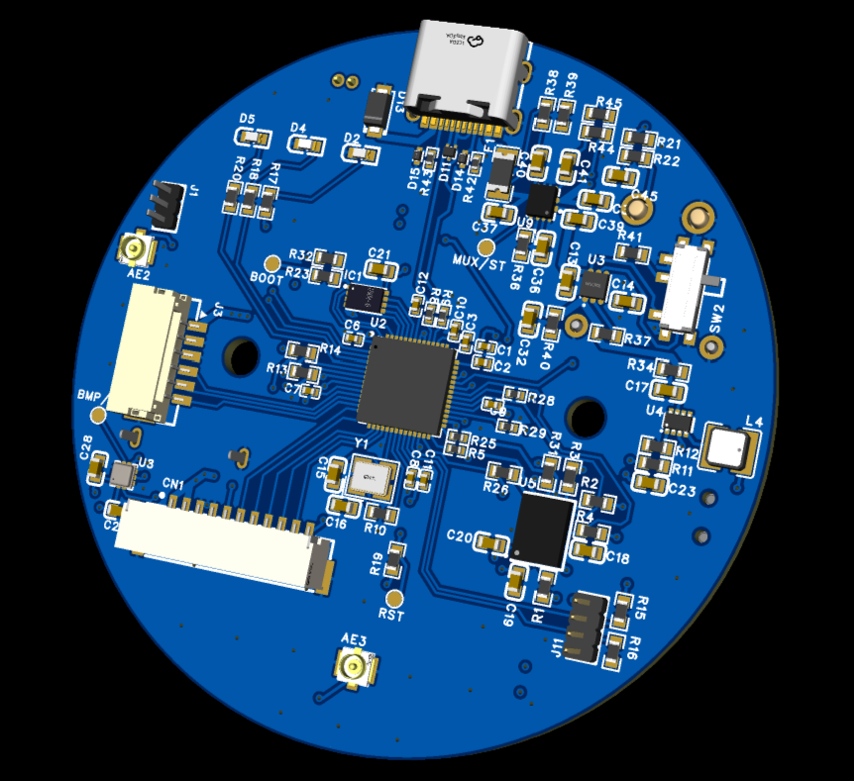
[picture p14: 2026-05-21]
hardware/mainboard/rev2/image/3d.png

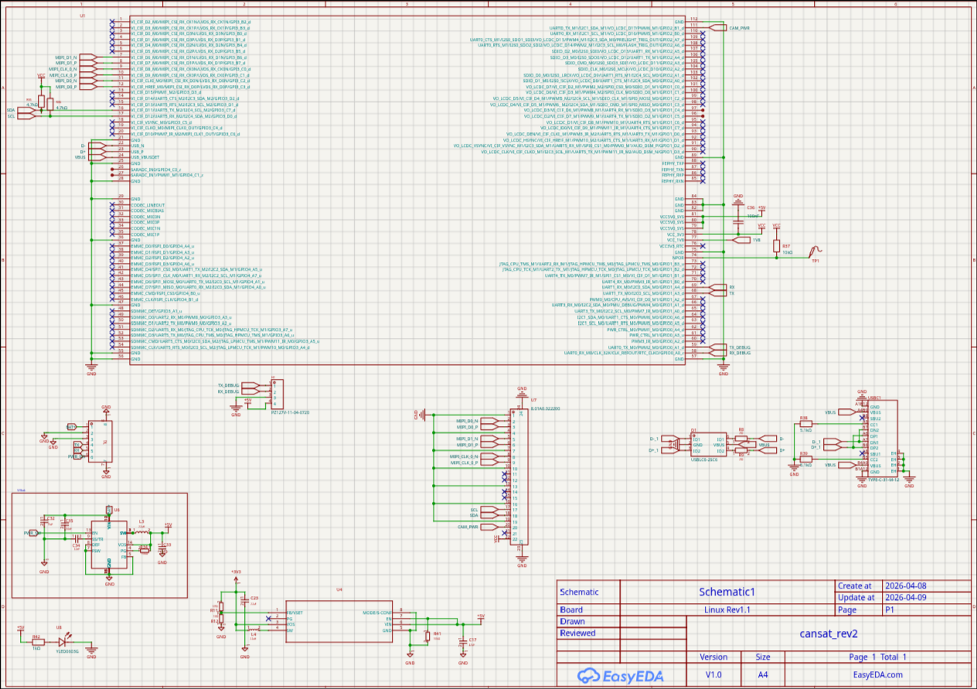
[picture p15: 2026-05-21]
hardware/linux-board/rev2/image/sch.png

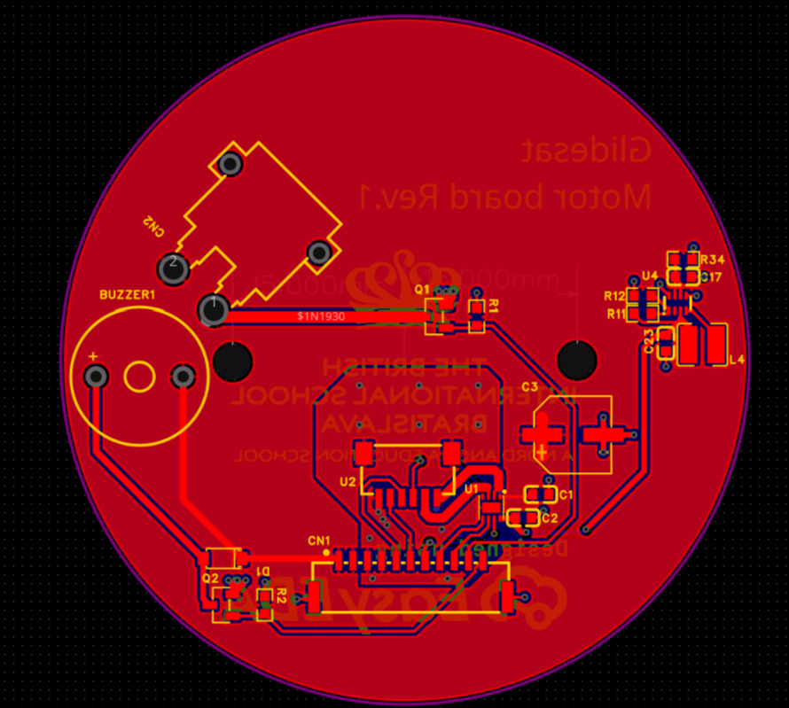
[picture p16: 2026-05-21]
hardware/motor-board/rev1/image/pcb.png

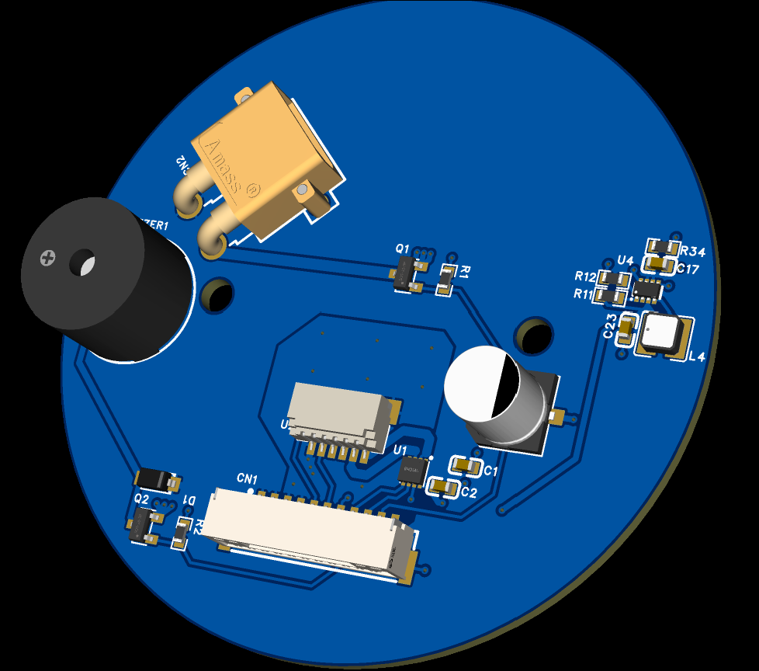
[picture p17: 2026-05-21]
hardware/motor-board/rev1/image/3d.png

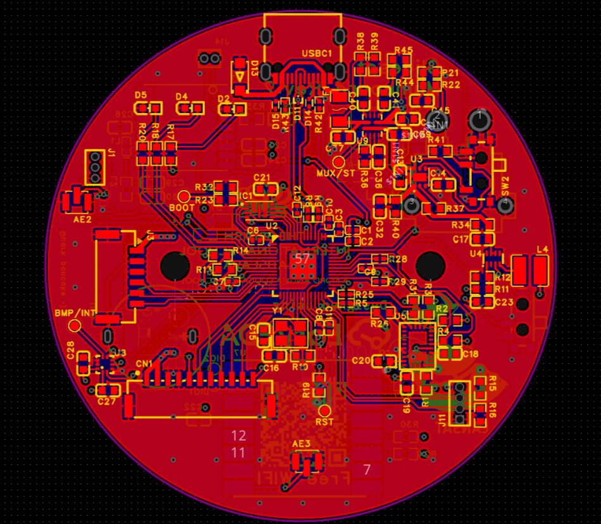
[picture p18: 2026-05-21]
hardware/mainboard/rev2/image/pcb.png

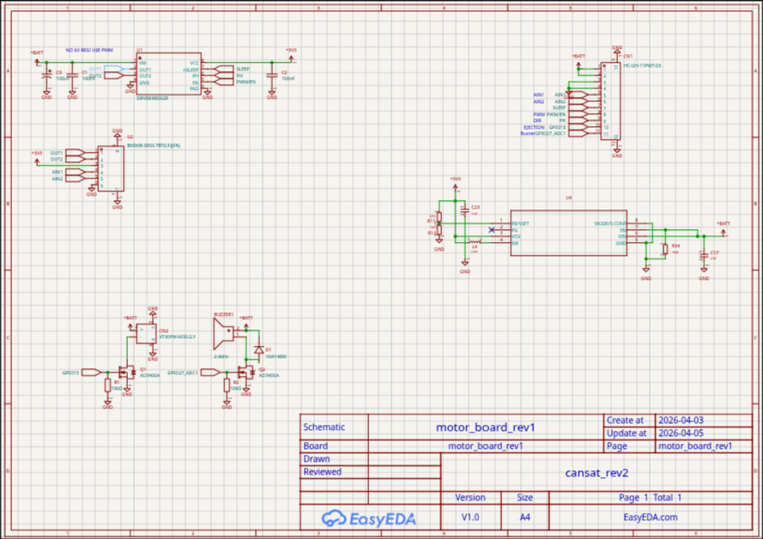
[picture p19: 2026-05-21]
hardware/motor-board/rev1/image/sch.png

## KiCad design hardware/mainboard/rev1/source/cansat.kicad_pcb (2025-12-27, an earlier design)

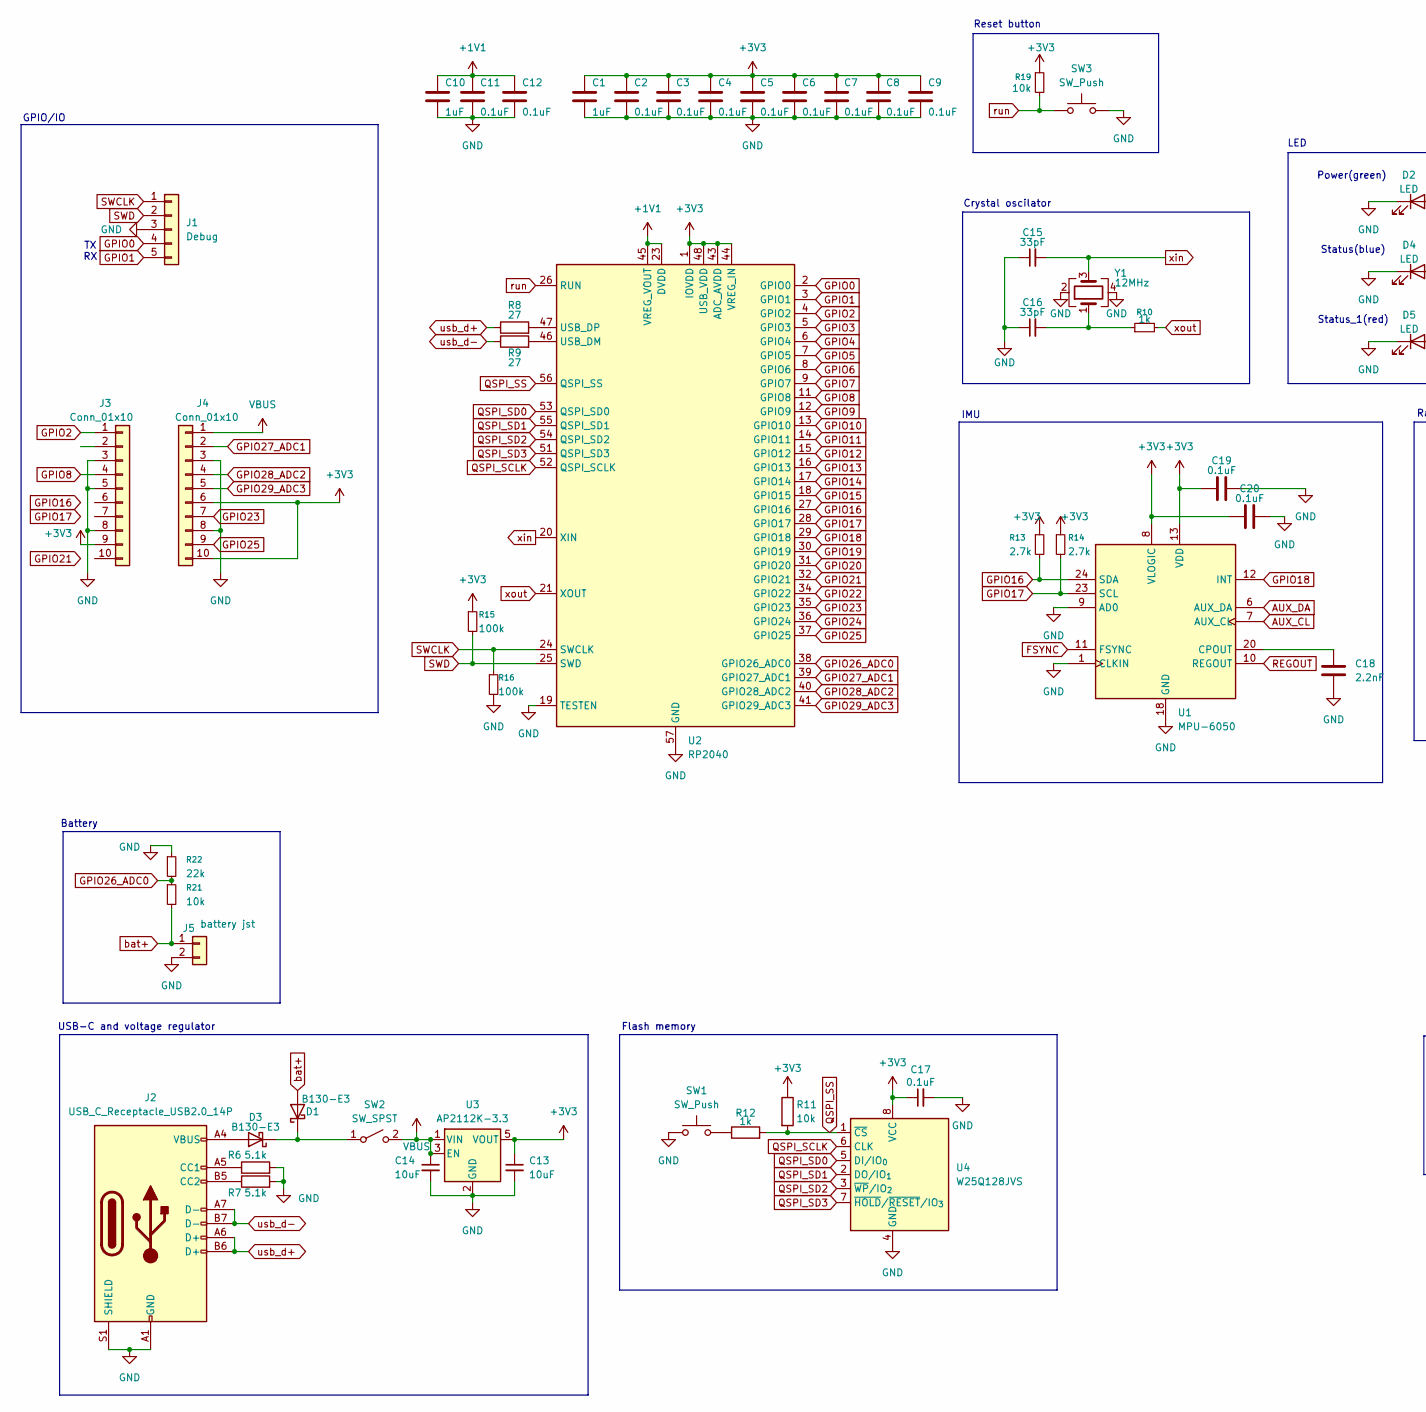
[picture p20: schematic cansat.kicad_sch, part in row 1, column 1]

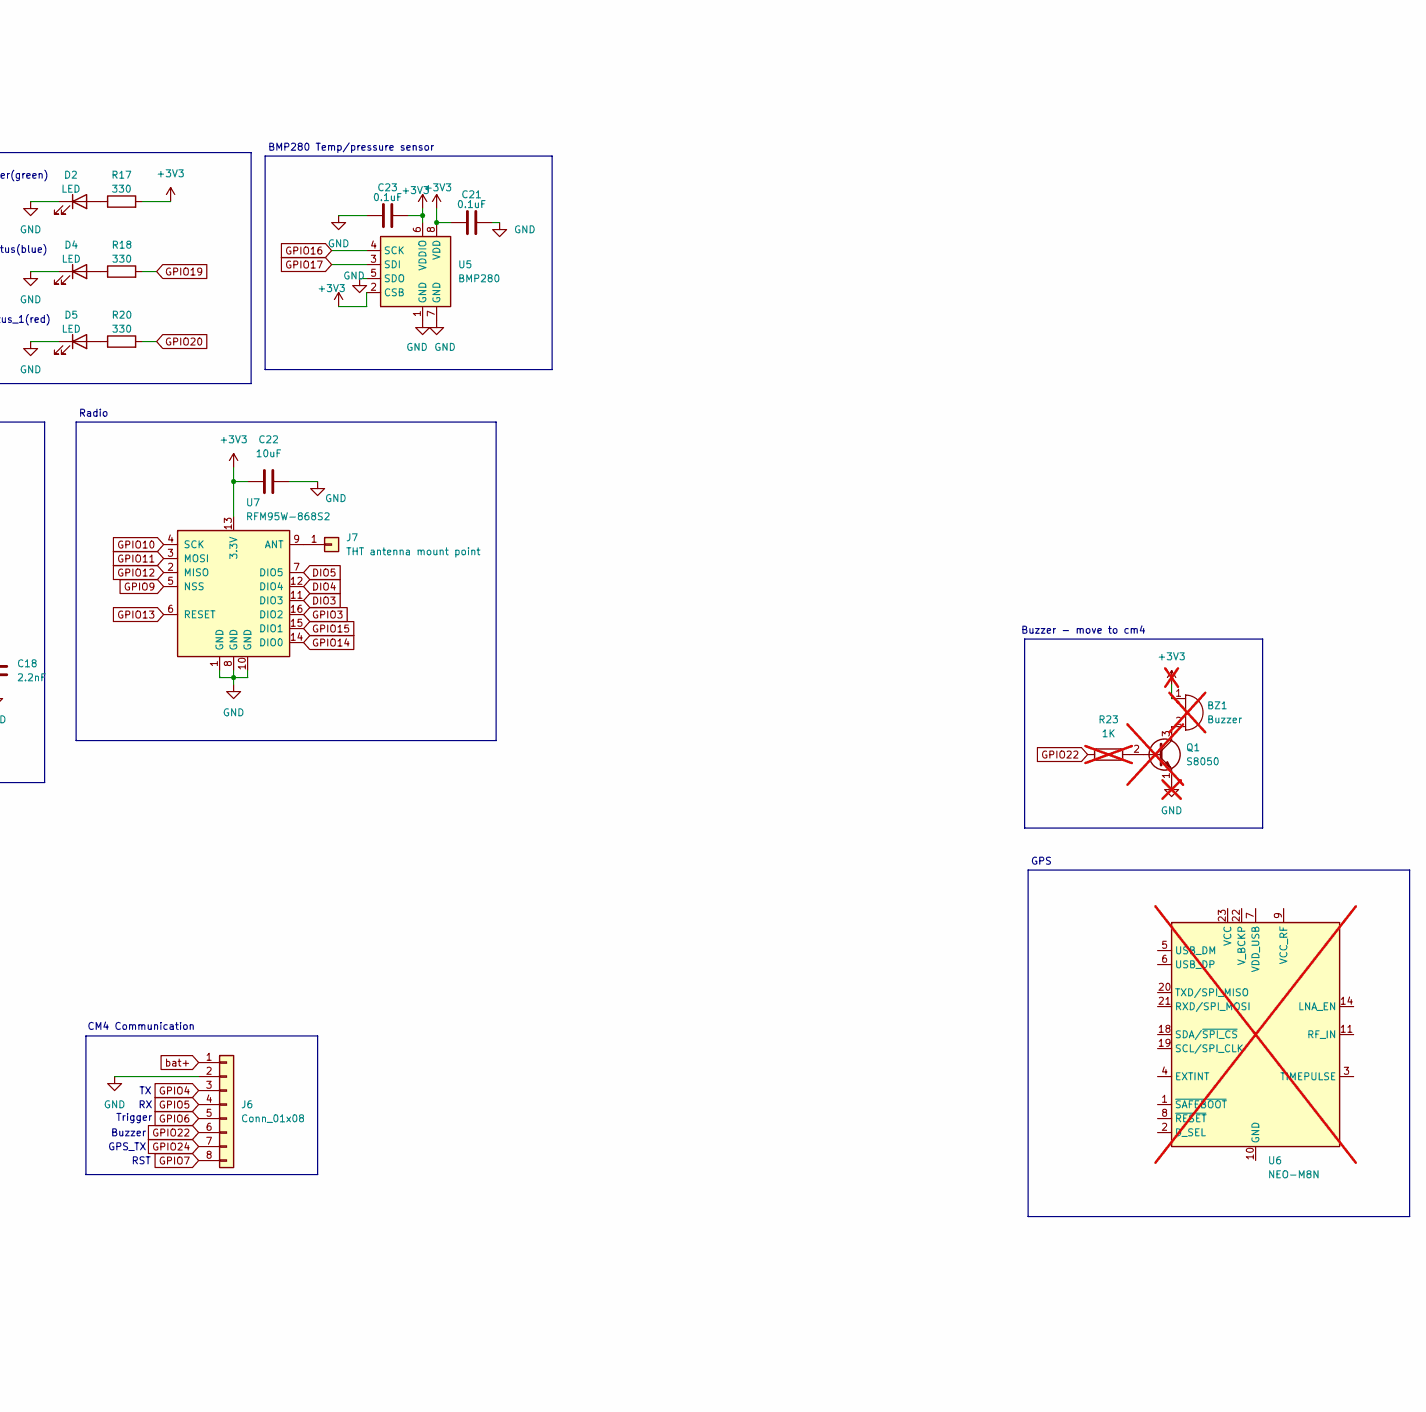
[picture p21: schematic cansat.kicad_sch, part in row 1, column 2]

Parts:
BZ1: Buzzer; not fitted
C1, C10: 1uF; C_0402_1005Metric_Pad0.74x0.62mm_HandSolder
C2, C3, C4, C5, C6, C7, C8, C9, C11, C12, C17, C19, C20, C21, C23: 0.1uF; C_0402_1005Metric_Pad0.74x0.62mm_HandSolder
C13, C14, C22: 10uF; C_0201_0603Metric_Pad0.64x0.40mm_HandSolder
C15, C16: 33pF; C_0402_1005Metric_Pad0.74x0.62mm_HandSolder
C18: 2.2nF; C_0402_1005Metric_Pad0.74x0.62mm_HandSolder
D1, D3: B130-E3; D_SOD-123
D2, D4, D5: LED; LED_0603_1608Metric_Pad1.05x0.95mm_HandSolder
J1: Debug; PinHeader_1x05_P2.00mm_Vertical
J2: USB_C_Receptacle_USB2.0_14P; USB_C_Receptacle_HRO_TYPE-C-31-M-12
J3, J4: Conn_01x10; PinHeader_1x10_P2.00mm_Vertical
J5: battery jst; JST_PH_S2B-PH-K_1x02_P2.00mm_Horizontal
J6: Conn_01x08; JST_GH_BM08B-GHS-TBT_1x08-1MP_P1.25mm_Vertical
J7: THT antenna mount point; PinHeader_1x01_P1.00mm_Vertical
Q1: S8050; TO-92_Inline; not fitted
R6, R7: 5.1k; C_0603_1608Metric_Pad1.08x0.95mm_HandSolder
R8, R9: 27; R_0402_1005Metric_Pad0.72x0.64mm_HandSolder
R10, R12: 1k; R_0402_1005Metric_Pad0.72x0.64mm_HandSolder
R11, R19: 10k; R_0402_1005Metric_Pad0.72x0.64mm_HandSolder
R13, R14: 2.7k; R_0402_1005Metric_Pad0.72x0.64mm_HandSolder
R15, R16: 100k; R_0402_1005Metric_Pad0.72x0.64mm_HandSolder
R17, R18, R20: 330; C_0603_1608Metric_Pad1.08x0.95mm_HandSolder
R21: 10k; C_0603_1608Metric_Pad1.08x0.95mm_HandSolder
R22: 22k; C_0603_1608Metric_Pad1.08x0.95mm_HandSolder
R23: 1K; not fitted
SW1, SW3: SW_Push; SW_Push_SPST_NO_Alps_SKRK
SW2: SW_SPST; SW_SPDT_PCM12
U1: MPU-6050; InvenSense_QFN-24_4x4mm_P0.5mm
U2: RP2040; QFN-56-1EP_7x7mm_P0.4mm_EP3.2x3.2mm
U3: AP2112K-3.3; SOT-23-5
U4: W25Q128JVS; Winbond_USON-8-1EP_3x2mm_P0.5mm_EP0.2x1.6mm
U5: BMP280; Bosch_LGA-8_2x2.5mm_P0.65mm_ClockwisePinNumbering
U6: NEO-M8N; ublox_NEO; not fitted
U7: RFM95W-868S2; XCVR_RFM95W-868S2
Y1: 12MHz; Crystal_SMD_3225-4Pin_3.2x2.5mm_HandSoldering

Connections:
+1V1: C10.1, C11.1, C12.1, U2.23 (DVDD), U2.45 (VREG_VOUT), U2.50 (DVDD)
+3V3: BZ1.1 (+), C1.1, C2.1, C3.1, C4.1, C5.1, C6.1, C7.1, C8.1, C9.1, C13.1, C17.1, C19.1, C20.1, C21.1, C22.2, C23.2, J3.9, J4.6, J4.10, R11.1, R13.1, R14.1, R15.1, R17.2, R19.1, U1.8 (VLOGIC), U1.13 (VDD), U2.1 (IOVDD), U2.10 (IOVDD), U2.22 (IOVDD), U2.33 (IOVDD), U2.42 (IOVDD), U2.43 (ADC_AVDD), U2.44 (VREG_IN), U2.48 (USB_VDD), U2.49 (IOVDD), U3.5 (VOUT), U4.8 (VCC), U5.2 (CSB), U5.6 (VDDIO), U5.8 (VDD), U7.13 (3.3V)
AUX_CL: U1.7 (AUX_CL)
AUX_DA: U1.6 (AUX_DA)
DIO3: U7.11 (DIO3)
DIO4: U7.12 (DIO4)
DIO5: U7.7 (DIO5)
FSYNC: U1.11 (FSYNC)
GND: C1.2, C2.2, C3.2, C4.2, C5.2, C6.2, C7.2, C8.2, C9.2, C10.2, C11.2, C12.2, C13.2, C14.2, C15.1, C16.1, C17.2, C18.2, C19.2, C20.2, C21.2, C22.1, C23.1, D2.1 (K), D4.1 (K), D5.1 (K), J1.3, J2.A1 (GND), J2.A12 (GND), J2.B1 (GND), J2.B12 (GND), J2.S1 (SHIELD), J3.3, J3.5, J3.8, J4.3, J4.8, J5.2, J6.2, Q1.1 (E), R6.2, R7.2, R16.2, R22.1, SW1.1, SW3.2, U1.1 (CLKIN), U1.9 (AD0), U1.18 (GND), U2.19 (TESTEN), U2.57 (GND), U3.2 (GND), U4.4 (GND), U5.1 (GND), U5.5 (SDO), U5.7 (GND), U7.1 (GND), U7.8 (GND), U7.10 (GND), Y1.2, Y1.4
GPIO0: J1.4, U2.2 (GPIO0)
GPIO1: J1.5, U2.3 (GPIO1)
GPIO2: J3.1, U2.4 (GPIO2)
GPIO3: U2.5 (GPIO3), U7.16 (DIO2)
GPIO4: J6.3, U2.6 (GPIO4)
GPIO5: J6.4, U2.7 (GPIO5)
GPIO6: J6.5, U2.8 (GPIO6)
GPIO7: J6.8, U2.9 (GPIO7)
GPIO8: J3.4, U2.11 (GPIO8)
GPIO9: U2.12 (GPIO9), U7.5 (NSS)
GPIO10: U2.13 (GPIO10), U7.4 (SCK)
GPIO11: U2.14 (GPIO11), U7.3 (MOSI)
GPIO12: U2.15 (GPIO12), U7.2 (MISO)
GPIO13: U2.16 (GPIO13), U7.6 (RESET)
GPIO14: U2.17 (GPIO14), U7.14 (DIO0)
GPIO15: U2.18 (GPIO15), U7.15 (DIO1)
GPIO16: R13.2, U1.24 (SDA), U2.27 (GPIO16), U5.4 (SCK)
GPIO17: R14.2, U1.23 (SCL), U2.28 (GPIO17), U5.3 (SDI)
GPIO18: U1.12 (INT), U2.29 (GPIO18)
GPIO19: R18.2, U2.30 (GPIO19)
GPIO20: R20.2, U2.31 (GPIO20)
GPIO21: U2.32 (GPIO21)
GPIO22: J6.6, R23.1, U2.34 (GPIO22)
GPIO23: J4.7, U2.35 (GPIO23)
GPIO24: J6.7, U2.36 (GPIO24)
GPIO25: J4.9, U2.37 (GPIO25)
GPIO26_ADC0: R21.1, R22.2, U2.38 (GPIO26_ADC0)
GPIO27_ADC1: J4.2, U2.39 (GPIO27_ADC1)
GPIO28_ADC2: J4.4, U2.40 (GPIO28_ADC2)
GPIO29_ADC3: J4.5, U2.41 (GPIO29_ADC3)
unnamed: BZ1.2 (-), Q1.3 (C)
unnamed: C16.2, R10.1, Y1.1
unnamed: D1.1 (K), D3.1 (K), SW2.1 (A)
unnamed: D2.2 (A), R17.1
unnamed: D3.2 (A), J2.A4 (VBUS), J2.A9 (VBUS), J2.B4 (VBUS), J2.B9 (VBUS)
unnamed: D4.2 (A), R18.1
unnamed: D5.2 (A), R20.1
unnamed: J2.A5 (CC1), R6.1
unnamed: J2.B5 (CC2), R7.1
unnamed: J7.1, U7.9 (ANT)
unnamed: Q1.2 (B), R23.2
unnamed: R12.1, SW1.2
unnamed: C18.1, U1.20 (CPOUT)
unnamed: R9.2, U2.46 (USB_DM)
unnamed: R8.2, U2.47 (USB_DP)
unnamed: U6.10 (GND), U6.12 (GND), U6.13 (GND), U6.24 (GND)
QSPI_SCLK: U2.52 (QSPI_SCLK), U4.6 (CLK)
QSPI_SD0: U2.53 (QSPI_SD0), U4.5 (DI/IO_{0})
QSPI_SD1: U2.55 (QSPI_SD1), U4.2 (DO/IO_{1})
QSPI_SD2: U2.54 (QSPI_SD2), U4.3 (~WP/IO_{2})
QSPI_SD3: U2.51 (QSPI_SD3), U4.7 (~HOLD/~RESET/IO_{3})
QSPI_SS: R11.2, R12.2, U2.56 (QSPI_SS), U4.1 (~CS)
REGOUT: U1.10 (REGOUT)
SWCLK: J1.1, R16.1, U2.24 (SWCLK)
SWD: J1.2, R15.2, U2.25 (SWD)
VBUS: C14.1, J4.1, SW2.2 (B), U3.1 (VIN), U3.3 (EN)
bat+: D1.2 (A), J5.1, J6.1, R21.2
run: R19.2, SW3.1, U2.26 (RUN)
usb_d+: J2.A6 (D+), J2.B6 (D+), R8.1
usb_d-: J2.A7 (D-), J2.B7 (D-), R9.1
xin: C15.2, U2.20 (XIN), Y1.3
xout: R10.2, U2.21 (XOUT)

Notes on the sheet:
Crystal oscilator
Trigger
Status(blue)
LED
GPS_TX
Battery
Radio
CM4 Communication
GPIO/IO
GPS
Buzzer
Reset button
RST
BMP280 Temp/pressure sensor
Status_1(red)
Power(green)
Buzzer - move to cm4
Flash memory
USB-C and voltage regulator
IMU

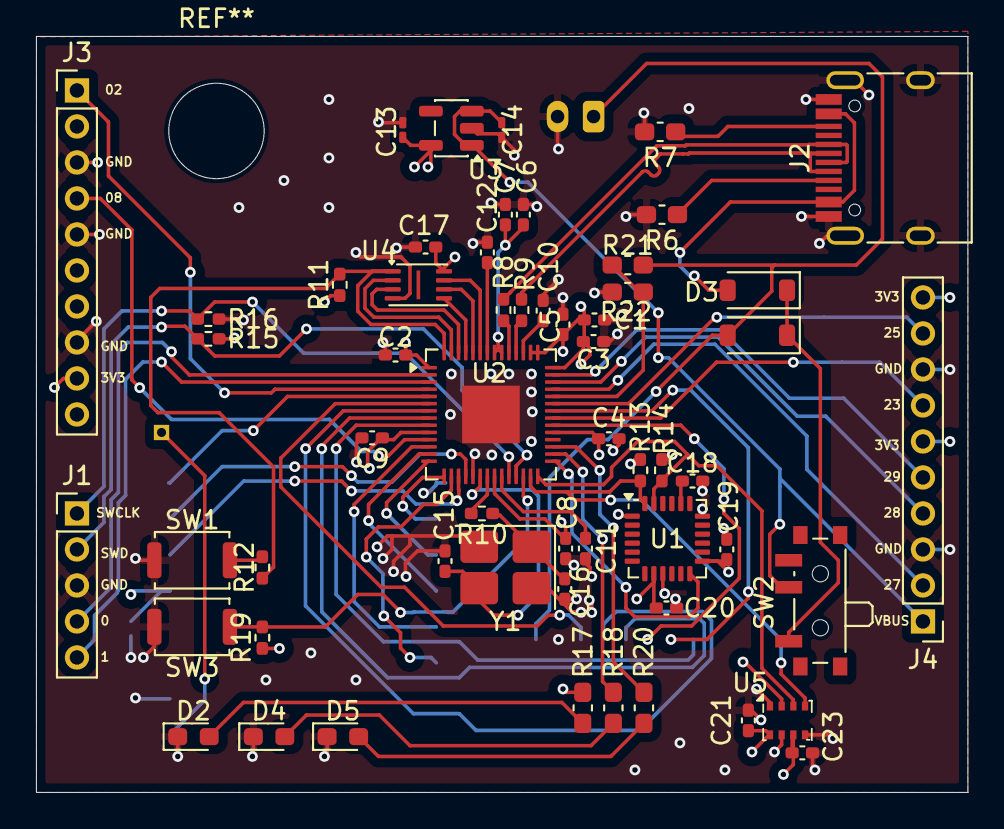
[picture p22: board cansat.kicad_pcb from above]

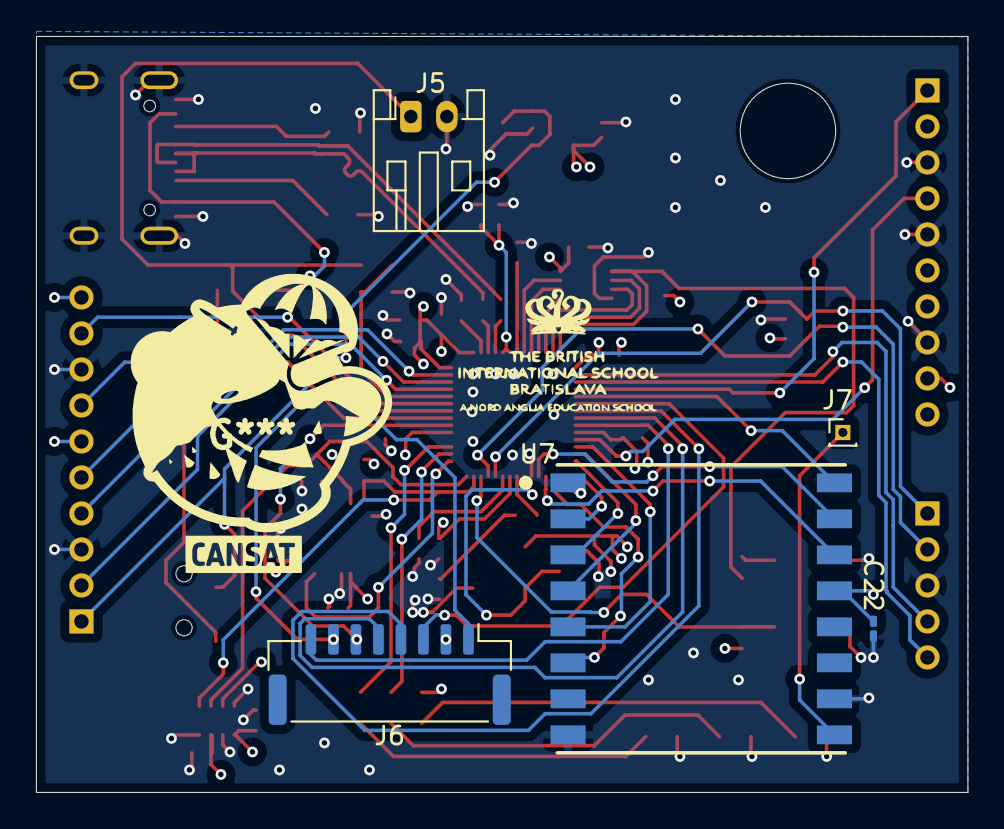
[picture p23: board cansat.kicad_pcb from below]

Board: 4 copper layers, 51.8 x 42.0 mm, 62 parts (5 on the bottom side), 60 nets.

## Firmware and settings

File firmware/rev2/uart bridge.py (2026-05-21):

# test code using micropython for UART bridge.

import machine
import sys


en_pin = machine.Pin(10, machine.Pin.OUT)
en_pin.value(1)

led = machine.Pin(2, machine.Pin.OUT)
led.value(1)

led = machine.Pin(3, machine.Pin.OUT)
led.value(1)




uart = machine.UART(0, 115200, tx=0, rx=1)
print("UART bridge running")

while True:
    if uart.any():
        data = uart.read()
        sys.stdout.write(data.decode('utf-8', errors='ignore'))

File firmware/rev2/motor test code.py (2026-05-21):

# test code using micropython to verify motor circuit functionality.

import machine

en_pin = machine.Pin(10, machine.Pin.OUT)
en_pin.value(1)

led = machine.Pin(2, machine.Pin.OUT)
led.value(1)

led = machine.Pin(3, machine.Pin.OUT)
led.value(1)

"""
motor and encoder test
RP2040, DRV8838DSGR

pin map
  ph(dir)       - GPIO14
  en(pwm)       - GPIO13
  sleep         - GPIO28
  enc a         - GPIO11
  enc b         - GPIO12
"""

from machine import Pin, PWM
import time

# pin set
ph    = Pin(14, Pin.OUT)                        # dir
en    = PWM(Pin(13), freq=20_000, duty_u16=0)   # pwm
sleep = Pin(28, Pin.OUT)                        # en

enc_a = Pin(11, Pin.IN, Pin.PULL_UP)            # enc a
enc_b = Pin(12, Pin.IN, Pin.PULL_UP)            # enc b

sleep.value(1)


# encoder counter                                                     #

position = 0

def encoder_isr(pin):
    global position
    if enc_b.value():
        position += 1
    else:
        position -= 1

enc_a.irq(trigger=Pin.IRQ_RISING, handler=encoder_isr)


def motor_forward(speed):
    """speed:0-100"""
    ph.value(0)
    en.duty_u16(int(speed / 100 * 65535))

def motor_reverse(speed):
    """speed 0-100"""
    ph.value(1)
    en.duty_u16(int(speed / 100 * 65535))

def motor_brake():
    en.duty_u16(0)

def motor_coast():
    en.duty_u16(0)
    sleep.value(0)

def motor_wake():
    sleep.value(1)

# test sequence

print("=" * 40)
print("DRV8838 + encoder")
print("=" * 40)

# 1 - forward increasing speed
print("\n1. forward 25% → 100%")
position = 0
for speed in [25, 50, 75, 100]:
    motor_forward(speed)
    time.sleep(1)
    print(f"speed {speed:3d}%, encoder count: {position}")

motor_brake()
time.sleep(0.5)

# 2 - reverse increasing speed
print("\n2 reverse ramp 25% → 100%")
position = 0
for speed in [25, 50, 75, 100]:
    motor_reverse(speed)
    time.sleep(1)
    print(f"speed {speed:3d}%, encoder count: {position}")

motor_brake()
time.sleep(0.5)

# 3 - brake, coast
print("\n3 brake test")
motor_forward(75)
time.sleep(1)
motor_brake()
print("brake applied, quick stop")
time.sleep(1)

print("\n4 coast test")
motor_forward(75)
time.sleep(1)
motor_coast()
print("coasting, spin down slowly")
time.sleep(2)
motor_wake()

# 4 - encoder acc 
print("\n5 encoder accuracy - forward 3 seconds")
position = 0
motor_forward(50)
time.sleep(3)
motor_brake()
print(f"encoder count after 3s at 50%: {position} ticks")

print("\n6 - encoder accuracy — reverse 3 seconds")
position = 0
motor_reverse(50)
time.sleep(3)
motor_brake()
print(f"encoder count after 3s at 50%: {position} ticks")

# --- Done ---
print("\n" + "=" * 40)
print("complete")
print("=" * 40)
en.deinit()

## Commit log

2025-12-28 BOM, Readme, images
    [BOM.csv]
2026-05-21 added all filed from new pcb(pro, source, image, review docs) and edited readme a bit.
    Journal needs to be added and readme needs to be edited for new revisions
    [cansat.kicad_pcb, cansat.kicad_sch]
